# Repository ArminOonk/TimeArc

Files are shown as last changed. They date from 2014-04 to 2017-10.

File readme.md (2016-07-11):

# Preparing the raspberry pi

## Update and install packages
Use the following commands to get the RPi ready

	sudo apt-get remove --purge desktop-base lightdm lxappearance lxde-common lxde-icon-theme lxinput lxpanel lxpolkit lxrandr lxsession-edit lxshortcut lxtask lxterminal
	sudo apt-get remove --purge obconf openbox raspberrypi-artwork 
	sudo apt-get remove --purge xarchiver xinit xserver-xorg 
	sudo apt-get remove --purge xserver-xorg-video-fbdev x11-utils x11-common x11-session utils
	sudo apt-get remove wolfram-*
	sudo apt-get update
	sudo apt-get upgrade
	sudo apt-get autoremove
	sudo rpi-update

# ESP Wifi
To get the esp wifi working first check the hardware. The APR2016 version has an error in the schematic. CH_PD is not connected to the correct pin.

In stall the driver using the instruction on the following website: http://oshlab.com/esp8266-raspberry-pi-gpio-wifi/

	cd ~
	git clone https://github.com/oshlab/esp8089.git
	cd esp8089
	sudo sh install
	sudo reboot
	sudo iwlist scan
	ifconfig

Check if wlan0 is visible. Now connect it to the wifi
	
	sudo nano /etc/wpa_supplicant/wpa_supplicant.conf

	network={
	ssid="testing"
	psk="testingPassword"
	}
	
Run the following commands if there is no internet connection (Test by using `ping 8.8.8.8`)

	sudo ifdown wlan0
	sudo ifup wlan0

# Install instructions

## Python packages
install pyfeed-0.7.4 and xe-0.7.4 from the Software directory

## Settings
Create a timearcPrivate.py file using the example

Add the following lines to /etc/rc.local

	sleep 30
	/home/pi/timearc/Software/startup

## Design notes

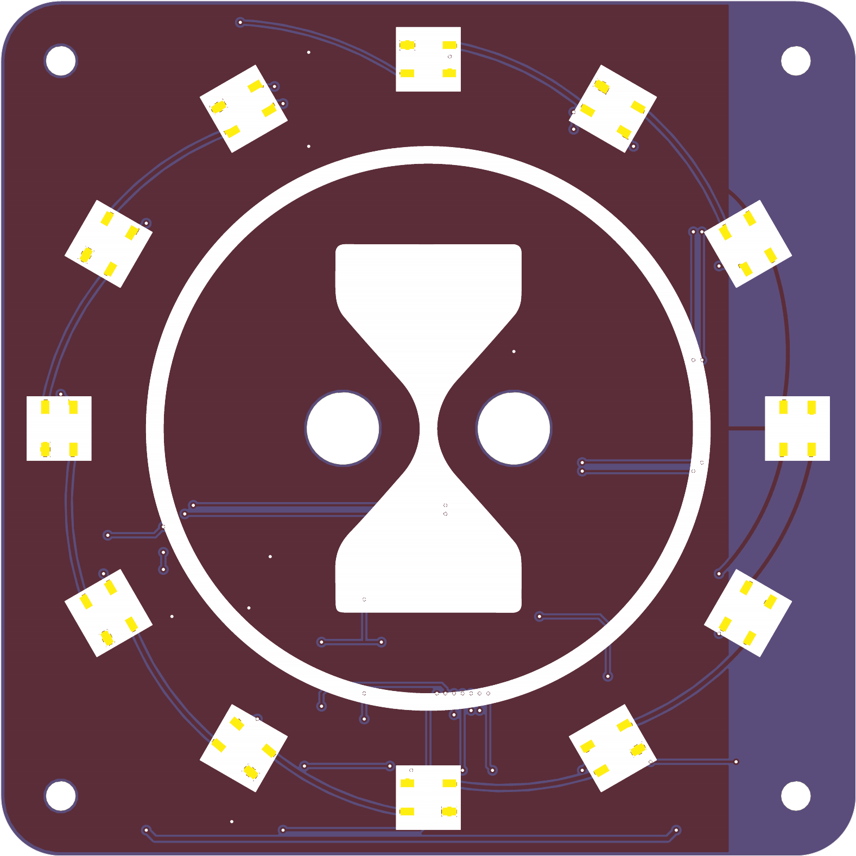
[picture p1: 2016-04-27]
Hardware/Back2016/Back2016_Bottom.png

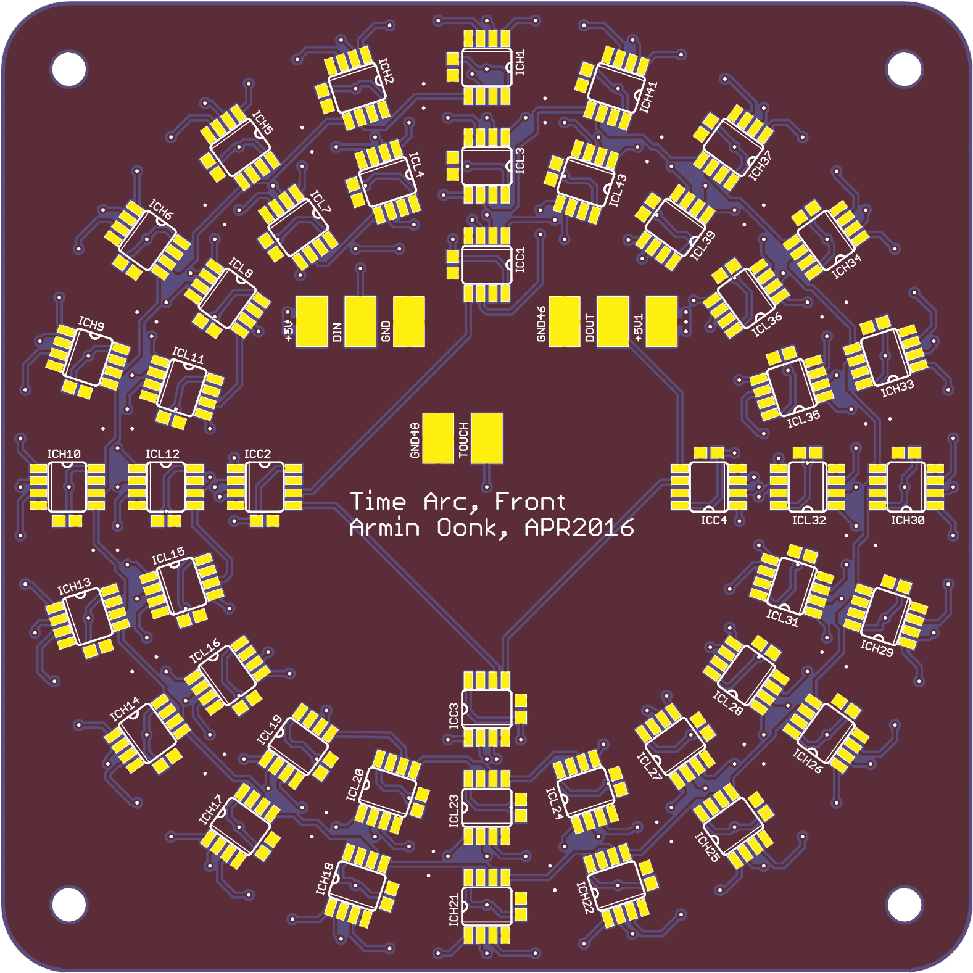
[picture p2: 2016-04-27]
Hardware/Front2016/Front2016_Top.png

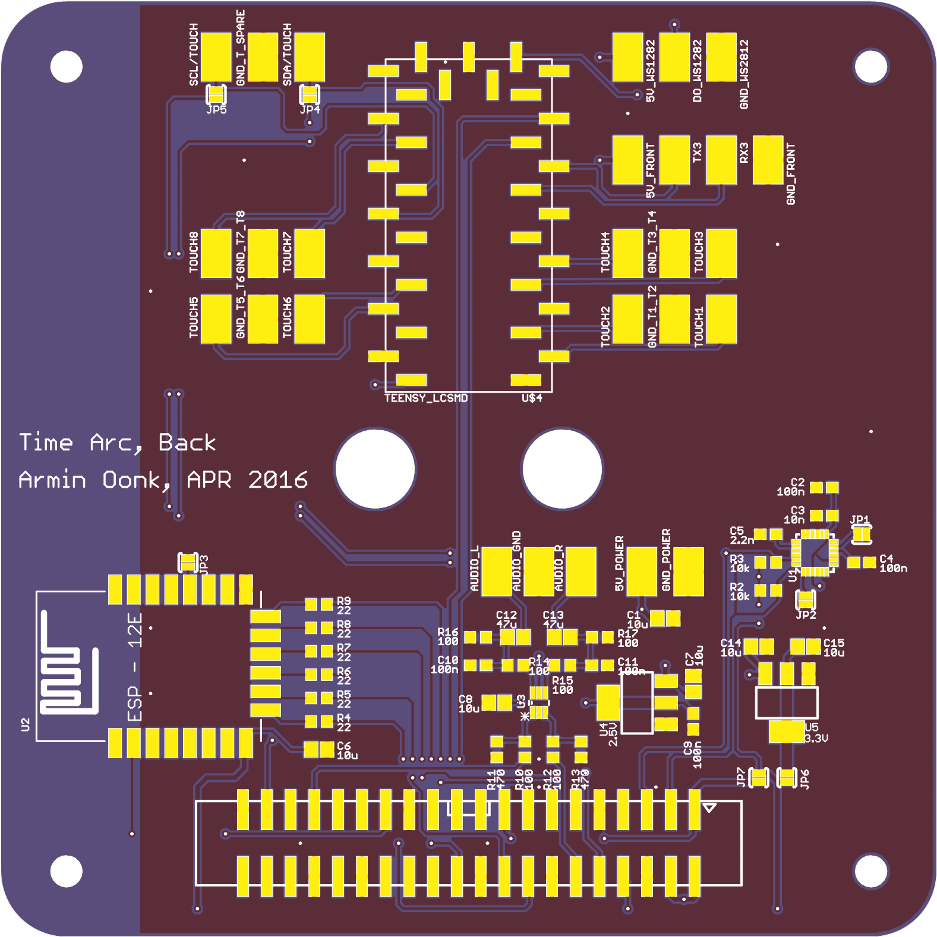
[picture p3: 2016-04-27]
Hardware/Back2016/Back2016_Top.png

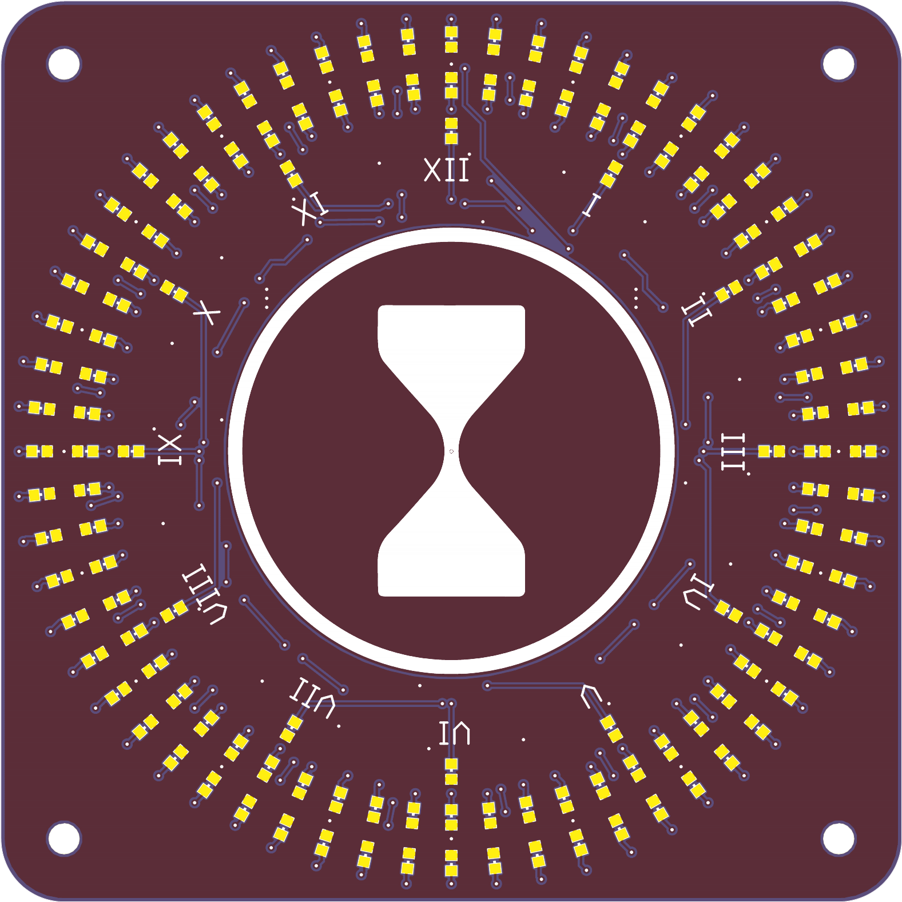
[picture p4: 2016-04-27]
Hardware/Front2016/Front2016_Bottom.png

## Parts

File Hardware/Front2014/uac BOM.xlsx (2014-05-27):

Qty | Part | Value | Description | MPN | OC_DIGIKEY_1 | OC_FARNELL | U_PRICE_1 | Price total
1 | C1 | 100n | CAPACITOR, European symbol |  |  | 1759016 | €0.01 | €0.01
1 | C2 | 100n | CAPACITOR, European symbol |  |  | 1759016 | €0.01 | €0.01
1 | C3 | 100n | CAPACITOR, European symbol |  |  | 1759016 | €0.01 | €0.01
1 | C4 | 100n | CAPACITOR, European symbol |  |  | 1759016 | €0.01 | €0.01
1 | C5 | 100n | CAPACITOR, European symbol |  |  | 1759016 | €0.01 | €0.01
1 | C6 | 6.8p | CAPACITOR, European symbol |  |  | 1856099 | €0.03 | €0.03
1 | C7 | 6.8p | CAPACITOR, European symbol |  |  | 1856099 | €0.03 | €0.03
1 | C8 | 10u | CAPACITOR, European symbol |  |  | 1759393 | €0.12 | €0.12
1 | C11 | 100n | CAPACITOR, European symbol |  |  | 1759016 | €0.01 | €0.01
1 | C17 | 10u | CAPACITOR, European symbol |  |  | 1759393 | €0.12 | €0.12
1 | C18 | 100n | CAPACITOR, European symbol |  |  | 1759016 | €0.01 | €0.01
1 | C20 | 10n | CAPACITOR, European symbol |  |  | 1759102 | €0.01 | €0.01
1 | C23 | 10u | CAPACITOR, European symbol |  |  | 1759393 | €0.12 | €0.12
1 | C24 | 100u | POLARIZED CAPACITOR, European symbol |  |  | 1907361 | €1.84 | €1.84
1 | C25 | 100u | POLARIZED CAPACITOR, European symbol |  |  | 1907361 | €1.84 | €1.84
1 | C27 | 10u | CAPACITOR, European symbol |  |  | 1759393 | €0.12 | €0.12
1 | FTDI |  | Header 6 |  |  | 2084270 | €1.22 | €1.22
12 | HOUR0 |  | LED |  |  | 8529841 | €0.28 | €3.36
1 | IC1 |  | Voltage Regulator LM1117 |  |  | 1469051 | €1.23 | €1.23
60 | MIN0 |  | LED |  |  | 8529868 | €0.20 | €12.00
1 | PROG |  | PIN HEADER |  |  | 2056005 | €0.45 | €0.45
1 | Q1 | 2N7002CK4SST | N-Channel JFETs |  |  | 1829183 | €0.37 | €0.37
1 | Q6 | 2N7002CK4SST | N-Channel JFETs |  |  | 1798076 | €0.02 | €0.02
1 | Q7 | 2N7002CK4SST | N-Channel JFETs |  |  | 1798076 | €0.02 | €0.02
1 | R1 |  | RESISTOR, European symbol |  |  | 2073347 | €0.01 | €0.01
1 | R2 |  | RESISTOR, European symbol |  |  | 2073347 | €0.01 | €0.01
1 | R3 |  | RESISTOR, European symbol |  |  | 2073347 | €0.01 | €0.01
1 | R4 |  | RESISTOR, European symbol |  |  | 2073347 | €0.01 | €0.01
1 | R5 |  | RESISTOR, European symbol |  |  | 2073347 | €0.01 | €0.01
1 | R6 |  | RESISTOR, European symbol |  |  | 2073347 | €0.01 | €0.01
1 | R7 |  | RESISTOR, European symbol |  |  | 2073347 | €0.01 | €0.01
1 | R8 |  | RESISTOR, European symbol |  |  | 2073347 | €0.01 | €0.01
1 | R9 |  | RESISTOR, European symbol |  |  | 2073347 | €0.01 | €0.01
1 | R10 |  | RESISTOR, European symbol |  |  | 2073347 | €0.01 | €0.01
1 | R11 |  | RESISTOR, European symbol |  |  | 2073347 | €0.01 | €0.01
1 | R12 |  | RESISTOR, European symbol |  |  | 2073347 | €0.01 | €0.01
1 | R13 | 0 | RESISTOR, European symbol |  |  | 2309106 | €0.0047 | €0.0047
1 | R16 | 10k | RESISTOR, European symbol |  |  | 1469748 | €0.02 | €0.02
1 | R23 | 10k | RESISTOR, European symbol |  |  | 1469748 | €0.02 | €0.02
1 | R27 | 10k | RESISTOR, European symbol |  |  | 1469748 | €0.02 | €0.02
1 | R28 | 0 | RESISTOR, European symbol |  |  | 2309106 | €0.0047 | €0.0047
1 | R29 | 0 | RESISTOR, European symbol |  |  | 2309106 | €0.0047 | €0.0047
1 | R30 | 1k5 | RESISTOR, European symbol |  |  | 2073391 | €0.01 | €0.01
1 | R31 | 10k | RESISTOR, European symbol |  |  | 1469748 | €0.02 | €0.02
1 | R32 | 10k | RESISTOR, European symbol |  |  | 1469748 | €0.02 | €0.02
1 | R33 | 36k | RESISTOR, European symbol |  |  | 2138459 | €0.01 | €0.01
1 | R34 | 47k | RESISTOR, European symbol |  |  | 2073515 | €0.01 | €0.01
1 | R36 | 10k | RESISTOR, European symbol |  |  | 1469748 | €0.02 | €0.02
1 | R43 | 10k | RESISTOR, European symbol |  |  | 1469748 | €0.02 | €0.02
60 | SEC0 |  | LED |  |  | 2213649 | €0.20 | €11.94
60 |  |  |  |  |  | 2251459 | €0.09 | €5.52
60 |  |  |  |  |  | 2217978 | €0.13 | €8.04
1 | SPECIAL0 |  | LED |  |  |  |  | €0.00
1 | SPECIAL3 |  | LED |  |  |  |  | €0.00
1 | SPECIAL5 |  | LED |  |  |  |  | €0.00
1 | SPECIAL6 |  | LED |  |  |  |  | €0.00
1 | SPECIAL9 |  | LED |  |  |  |  | €0.00
1 | SPECIAL11 |  | LED |  |  |  |  | €0.00
1 | U$1 | STM32F103CBT6 |  |  |  | 1447640 | €5.71 | €5.71
1 | U$2 | CRYSTAL_32KHZ |  | MC-306 32.768K-E3:ROHS | SER2417TR-ND |  |  | €0.00
1 | U$11 | KDT0030 | Updated Light Sensor | KDT00030TR | KDT00030FSCT-ND |  | €0.60 | €0.60
1 | U$12 | USB-MINIB-5PIN | Mini-USB B" connector with 5th pin broken out." |  |  | 1125348 | €0.56 | €0.56
1 | U$13 | USBLC6-2SC6 |  | USBLC6-2SC6 |  | 1269406 | €0.76 | €0.76
1 | U2 | ADXL345 |  |  |  | 1853935 | €5.38 | €5.38
1 | Y1 | RESONATORSMD | Resonator |  | 490-1198-1-ND | 1615352 | €0.80 | €0.80
4 |  | spacers m3x40 |  |  |  | 1466833 | €0.48 | €1.92
 |  |  |  |  |  |  | Total | €64.46

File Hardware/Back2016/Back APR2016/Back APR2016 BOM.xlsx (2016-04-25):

Part | Value | Device | Description | Manufacturer | MPN | OC_FARNELL | Link
C1 | 10u | C-EUC0805 | CAPACITOR, European symbol |  |  | 2320856
C2 | 100n | C-EUC0603 | CAPACITOR, European symbol |  |  | 2496832
C3 | 10n | C-EUC0603 | CAPACITOR, European symbol |  |  | 2496826
C4 | 100n | C-EUC0603 | CAPACITOR, European symbol |  |  | 2496832
C5 | 2.2n | C-EUC0603 | CAPACITOR, European symbol |  |  | 2496845
C6 | 10u | C-EUC0805 | CAPACITOR, European symbol |  |  | 2320856
C7 | 10u | C-EUC0805 | CAPACITOR, European symbol |  |  | 2320856
C8 | 10u | C-EUC0805 | CAPACITOR, European symbol |  |  | 2320856
C9 | 100n | C-EUC0603 | CAPACITOR, European symbol |  |  | 2496832
C10 | 100n | C-EUC0603 | CAPACITOR, European symbol |  |  | 2496832
C11 | 100n | C-EUC0603 | CAPACITOR, European symbol |  |  | 2496832
C12 | 47u | C-EUC0805 | CAPACITOR, European symbol |  |  | 2362109
C13 | 47u | C-EUC0805 | CAPACITOR, European symbol |  |  | 2362109
C14 | 10u | C-EUC0805 | CAPACITOR, European symbol |  |  | 2320856
C15 | 10u | C-EUC0805 | CAPACITOR, European symbol |  |  | 2320856
J1 | RASPBERRYPI-40-PIN-GPIO-SMT | RASPBERRYPI-40-PIN-GPIO-SMT | Second Generation Raspberry Pi GPIO Header |  |  | 1256663
LED1 | WS2812B5050 | WS2812B5050 |  |  |  |  | http://www.aliexpress.com/item/10-1000pcs-WS2812B-4pins-5050-SMD-Black-White-version-WS2812-Individually-Addressable-Digital-RGB-LED-Chip/32453497583.html
LED2 | WS2812B5050 | WS2812B5050 |  |  |  |  | http://www.aliexpress.com/item/10-1000pcs-WS2812B-4pins-5050-SMD-Black-White-version-WS2812-Individually-Addressable-Digital-RGB-LED-Chip/32453497583.html
LED3 | WS2812B5050 | WS2812B5050 |  |  |  |  | http://www.aliexpress.com/item/10-1000pcs-WS2812B-4pins-5050-SMD-Black-White-version-WS2812-Individually-Addressable-Digital-RGB-LED-Chip/32453497583.html
LED4 | WS2812B5050 | WS2812B5050 |  |  |  |  | http://www.aliexpress.com/item/10-1000pcs-WS2812B-4pins-5050-SMD-Black-White-version-WS2812-Individually-Addressable-Digital-RGB-LED-Chip/32453497583.html
LED5 | WS2812B5050 | WS2812B5050 |  |  |  |  | http://www.aliexpress.com/item/10-1000pcs-WS2812B-4pins-5050-SMD-Black-White-version-WS2812-Individually-Addressable-Digital-RGB-LED-Chip/32453497583.html
LED6 | WS2812B5050 | WS2812B5050 |  |  |  |  | http://www.aliexpress.com/item/10-1000pcs-WS2812B-4pins-5050-SMD-Black-White-version-WS2812-Individually-Addressable-Digital-RGB-LED-Chip/32453497583.html
LED7 | WS2812B5050 | WS2812B5050 |  |  |  |  | http://www.aliexpress.com/item/10-1000pcs-WS2812B-4pins-5050-SMD-Black-White-version-WS2812-Individually-Addressable-Digital-RGB-LED-Chip/32453497583.html
LED8 | WS2812B5050 | WS2812B5050 |  |  |  |  | http://www.aliexpress.com/item/10-1000pcs-WS2812B-4pins-5050-SMD-Black-White-version-WS2812-Individually-Addressable-Digital-RGB-LED-Chip/32453497583.html
LED9 | WS2812B5050 | WS2812B5050 |  |  |  |  | http://www.aliexpress.com/item/10-1000pcs-WS2812B-4pins-5050-SMD-Black-White-version-WS2812-Individually-Addressable-Digital-RGB-LED-Chip/32453497583.html
LED10 | WS2812B5050 | WS2812B5050 |  |  |  |  | http://www.aliexpress.com/item/10-1000pcs-WS2812B-4pins-5050-SMD-Black-White-version-WS2812-Individually-Addressable-Digital-RGB-LED-Chip/32453497583.html
LED11 | WS2812B5050 | WS2812B5050 |  |  |  |  | http://www.aliexpress.com/item/10-1000pcs-WS2812B-4pins-5050-SMD-Black-White-version-WS2812-Individually-Addressable-Digital-RGB-LED-Chip/32453497583.html
LED12 | WS2812B5050 | WS2812B5050 |  |  |  |  | http://www.aliexpress.com/item/10-1000pcs-WS2812B-4pins-5050-SMD-Black-White-version-WS2812-Individually-Addressable-Digital-RGB-LED-Chip/32453497583.html
R2 | 10k | R-EU_R0603 | RESISTOR, European symbol |  |  | 1469748
R3 | 10k | R-EU_R0603 | RESISTOR, European symbol |  |  | 1469748
R4 | 22 | R-EU_R0603 | RESISTOR, European symbol |  |  | 9330844
R5 | 22 | R-EU_R0603 | RESISTOR, European symbol |  |  | 9330844
R6 | 22 | R-EU_R0603 | RESISTOR, European symbol |  |  | 9330844
R7 | 22 | R-EU_R0603 | RESISTOR, European symbol |  |  | 9330844
R8 | 22 | R-EU_R0603 | RESISTOR, European symbol |  |  | 9330844
R9 | 22 | R-EU_R0603 | RESISTOR, European symbol |  |  | 9330844
R10 | 100 | R-EU_R0603 | RESISTOR, European symbol |  |  | 2130776
R11 | 470 | R-EU_R0603 | RESISTOR, European symbol |  |  | 2447374
R12 | 100 | R-EU_R0603 | RESISTOR, European symbol |  |  | 2130776
R13 | 470 | R-EU_R0603 | RESISTOR, European symbol |  |  | 2447374
R14 | 100 | R-EU_R0603 | RESISTOR, European symbol |  |  | 2130776
R15 | 100 | R-EU_R0603 | RESISTOR, European symbol |  |  | 2130776
R16 | 100 | R-EU_R0603 | RESISTOR, European symbol |  |  | 2130776
R17 | 100 | R-EU_R0603 | RESISTOR, European symbol |  |  | 2130776
U$4 | TEENSY_LCSMD | TEENSY_LCSMD | Teensy LC |  |  | 2356213
U1 |  | MPU-9150QFN-24-NP | 9DOF (3mag, 3accel, 3rotat). I2C interface. |  |  |  | http://www.aliexpress.com/item/Free-shipping-1pcs-lot-MPU-9150-MPU9150/32565889824.html
U2 |  | ESP12ESMD | ESP12E Module |  |  |  | http://www.aliexpress.com/item/2015-New-version-1PCS-ESP-12F-ESP-12E-upgrade-ESP8266-remote-serial-Port-WIFI-wireless-module/32590584160.html
U3 | SN74LVC2G34DCKR | SN74LVC2G34DCKR | DUAL BUFFER GATE |  | SN74LVC2G34DCKR | 1595409
U4 | 2.5V | V_REG_LM1117SOT223 | Voltage Regulator LM1117 |  |  | 1564629
U5 | 3.3V | V_REG_LM1117SOT223 | Voltage Regulator LM1117 |  |  | 1469051
 |  |  | Power jack panel mount |  |  | 1216726
 |  |  | Jack 3.5 mm panel mount |  |  | 1267396
Solder PADS
5V_FRONT | SOLDER_PAD | SOLDER_PAD
5V_POWER | SOLDER_PAD | SOLDER_PAD
5V_WS1282 | SOLDER_PAD | SOLDER_PAD
AUDIO_GND | SOLDER_PAD | SOLDER_PAD
AUDIO_L | SOLDER_PAD | SOLDER_PAD
AUDIO_R | SOLDER_PAD | SOLDER_PAD
DO_WS1282 | SOLDER_PAD | SOLDER_PAD
GND_FRONT | SOLDER_PAD | SOLDER_PAD
GND_POWER | SOLDER_PAD | SOLDER_PAD
GND_T1_T2 | SOLDER_PAD | SOLDER_PAD
GND_T3_T4 | SOLDER_PAD | SOLDER_PAD
GND_T5_T6 | SOLDER_PAD | SOLDER_PAD
GND_T7_T8 | SOLDER_PAD | SOLDER_PAD
GND_T_SPARE | SOLDER_PAD | SOLDER_PAD
GND_WS2812 | SOLDER_PAD | SOLDER_PAD
RX3 | SOLDER_PAD | SOLDER_PAD
SCL/TOUCH | SOLDER_PAD | SOLDER_PAD
SDA/TOUCH | SOLDER_PAD | SOLDER_PAD
TOUCH1 | SOLDER_PAD | SOLDER_PAD
TOUCH2 | SOLDER_PAD | SOLDER_PAD
TOUCH3 | SOLDER_PAD | SOLDER_PAD
TOUCH4 | SOLDER_PAD | SOLDER_PAD
TOUCH5 | SOLDER_PAD | SOLDER_PAD
TOUCH6 | SOLDER_PAD | SOLDER_PAD
TOUCH7 | SOLDER_PAD | SOLDER_PAD
TOUCH8 | SOLDER_PAD | SOLDER_PAD
TX3 | SOLDER_PAD | SOLDER_PAD
Jumpers
JP1 | JUMPER-PAD-2-NOYES_SILK | JUMPER-PAD-2-NOYES_SILK
JP2 | JUMPER-PAD-2-NOYES_SILK | JUMPER-PAD-2-NOYES_SILK
JP3 | JUMPER-PAD-2-NOYES_SILK | JUMPER-PAD-2-NOYES_SILK
JP4 | JUMPER-PAD-2-NOYES_SILK | JUMPER-PAD-2-NOYES_SILK
JP5 | JUMPER-PAD-2-NOYES_SILK | JUMPER-PAD-2-NOYES_SILK
JP6 | JUMPER-PAD-2-NOYES_SILK | JUMPER-PAD-2-NOYES_SILK
JP7 | JUMPER-PAD-2-NOYES_SILK | JUMPER-PAD-2-NOYES_SILK

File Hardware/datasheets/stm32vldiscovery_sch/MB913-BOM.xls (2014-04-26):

MB913 BOM
NO | Code | Part Number | Manufacturer | Description | Designator | Quantity | Process | Note
1 | 3ST0003 |  | FASTPRINT | PCB,MB913C |  | 1 | SMT
2 | ADL0002 | 316102S111A | LWCONN | Short ,open 2.54MM,1UGold,LWCONN；Harwin,M7566-05/M7571-05 |  | 3 | ASS
3 | AKG0002 | SH-517 Blue | szalong | key Cap,Blue,MB672 | B1-1 | 1 | ASS
4 | AKG0003 | SH-517Black | szalong | key Cap,Black,MB672 | B2-1 | 1 | ASS
5 | CCC0009 | CC0603KRX5R7BB105 | YAGEO | Capacitance,1uF,10%,16V,X5R,0603 | C16 | 1 | SMT
6 | CCC0049 | CC0603JRNPO9BN200 | YAGEO | Capacitance,20pF,5%,50V,NPO,0603 | C13,C12,C8,C9 | 4 | SMT
7 | CCC0071 | CC0402KRX7R7BB104 | YAGEO | Capacitance,0.1uF,10%,16V,X7R,0402 | C18,C19 | 2 | SMT
8 | CCC0188 | CC0603CRNPO9BN6R8 | YAGEO | Capacitance，0603，NPO,50V ±0.25PF 6P8F | C17,C11 | 2 | SMT
9 | CCC0194 | CC0603KRX7R7BB104 | YAGEO | Capacitance,0.1uF,10%,16V,X7R,0603 | C23,C3,C21,C20, C15,C7,C4,C10,C6,C5 | 10 | SMT
10 | CTD0045 | TAJA105K016R | AVX | Tantalum capacitor,1uF,10%,16V,AType,AVX | C14 | 1 | SMT
11 | CTD0099 | TAJA106K016RNJ | AVX | Tantalum capacitor,10uF,10%,16V,AType,AVX | C1,C2 | 2 | SMT
12 | DEJ0018 | BZX84-C5V6 | NXP | Diode，BZX84-C5V6，5.6V,SOT23,NXP | D3,D4 | 2 | SMT
13 | DLD0027 | 19-213-RC-AP1Q2B-3T | EVERLIGHT | LED,red,0603,19-213-RC-AP1Q2B-3T,LED | LD2,LD1 | 2 | SMT
14 | DLD0028 | 19-213SY6C/5530-E2/TR8 | EVERLIGHT | LED,Green,0603,19-213SY6C/5530-E2/TR8,LED | LD3 | 1 | SMT
15 | DLD0029 | 19-217/BHC-ZL1M2RY/3T | EVERLIGHT | LED,blue,0603,19-217/BHC-ZL1M2RY/3T,LED | LD4 | 1 | SMT
16 | JJZ0001 | PIN-E740 | LWCONN | Stilt,7.4Circular apertureCrystal oscillatorFoot,1PIN,Golden,DIP,PIN-E740，LWCONN | X2-1，X2-2 | 2 | DIP
17 | JPZ0015 | 313140S212116 | LWCONN | Row,2.54mm,1*4,L=11.6,180Degree,3UGold,DIP,LWCONN | CN2,CN3 | 8/40 | DIP
18 | JPZ0015 | 313140S212116 | LWCONN | Row,2.54mm,1*2,L=11.6,180Degree,3UGold,DIP,LWCONN | JP1 | 2/40 | DIP
19 | JPZ0032 | 313128S212145 | LWCONN | Row,2.54mm,1*28P,180Degree,L=14.5,Plating3UGold,SMT,LWCONN | P1,P2 | 2 | SMT
20 | JPZ0033 | 313140S212145 | LWCONN | Row,2.54mm,1*6P,180Degree,L=14.5,Plating3UGold,SMT,LWCONN | P3 | 6/40 | SMT
21 | JUS0021 | MUSB5QS-BM1H6-NLB-E | townes | USB,MUSB5QS-BM1H6-NLB-E,townes | CN1 | 1 | SMT
22 | LCZ0006 | FCM1608KF-601T03 | Tai-tech | 600R,350mA,0603,FCM1608KF-601T03,Tai-tech | L1 | 1 | SMT
23 | PBQ0004 |  |  | label,18*6mm,MB913C | label | 1 | ASS
24 | PBQ0016 |  |  | Test label，CharacterT1,T2,T3,T4,QA,see Sample |  | 1 | ASS
25 | PKZ0003 |  |  | The ST standard cardboardMB913,93*135mm,STStandard Edition | packing | 1 | ASS
26 | PKZ0008 |  |  | The ST standard cardboardMB913,93*135mm,EBVEdition | packing | 1 | ASS
27 | PKZ0009 |  |  | The ST standard cardboardMB913,93*135mm,XL Edition | packing | 1 | ASS
28 | PKZ0010 |  |  | The ST standard cardboardMB913,93*135mm,ARROW Edition | packing | 1 | ASS
29 | PKZ0011 |  |  | The ST standard cardboardMB913,93*135mm,Silica Edition | packing | 1 | ASS
30 | PKZ0012 |  |  | The ST standard cardboardMB913,93*135mm,Farnell Edition | packing | 1 | ASS
31 | PSD0001 | TZ-211 |  | Label，Black text on a white background，6mm,8m | Label | 1/450 | ASS
32 | PXS0001 |  |  | MB913 blister,PET0.5mm, | packing | 1 | ASS
33 | PZB0001 |  |  | Cardboard，605*415mm | box | 1/50 | ASS
34 | PZX0006 |  |  | box，L620*425*310mm | box | 150/1 | ASS
35 | RRC0023 | RC0805JR-070RL | YAGEO | Resistance,0R,5%,0805 | R22 | 1 | SMT
36 | RRC0029 | RC0603JR-07100RL | YAGEO | Resistance,100R,1%,0603 | R20 | 1 | SMT
37 | RRC0030 | RC0603JR-070RL | YAGEO | Resistance,0R,5%,0603 | R15 | 1 | SMT
38 | RRC0220 | RC0402JR-070RL | YAGEO | Resistance,0R,5%,0402 | SB1,SB2,SB3,SB5,SB7,SB9,SB11,SB16,SB17,SB18 | 10 | SMT
39 | RRC0224 | RC0402JR-071K5L | YAGEO | Resistance,1.5K,1%,0402 | R2 | 1 | SMT
40 | RRC0301 | RC0402JR-0722RL | YAGEO | Resistance,22R,1%,0402 | R4,R3,R11,R12 | 4 | SMT
41 | RRC0328 | RC0603FR-07665RL | YAGEO | Resistance，665R,1%,0603 | R26 | 1 | SMT
42 | RRC0374 | RC0603JR-07820RL | YAGEO | Resistance,820R,1%,0603 | R23 | 1 | SMT
43 | RRC0379 | RC0603JR-07100KL | YAGEO | Resistance,100K,1%,0603 | R1 | 1 | SMT
44 | RRC0387 | RC0603JR-07330RL | YAGEO | Resistance,330R,1%,0603 | R25 | 1 | SMT
45 | RRC0388 | RC0603JR-07220KL | YAGEO | Resistance,220K,1%,0603 | R21 | 1 | SMT
46 | RRC0402 | RC0402JR-074K7L | YAGEO | Resistance,4.7K,1%,0402 | R9,R10 | 2 | SMT
47 | RRC0403 | RC0603JR-07510RL | YAGEO | Resistance,510R,1%,0603 | R18,R16,R6 | 3 | SMT
48 | RRC0404 | RC0603JR-07220RL | YAGEO | Resistance,220R,1%,0603 | R14 | 1 | SMT
49 | RRC0411 | RC0402JR-071KL | YAGEO | Resistance,1K,1%,0402 | R5 | 1 | SMT
50 | RRC0412 | RC0402JR-07100KL | YAGEO | Resistance,100K,1%,0402 | R7,R13 | 2 | SMT
51 | RRC0413 | RC0402JR-0710KL | YAGEO | Resistance,10K,1%,0402 | R19,R17,R8 | 3 | SMT
52 | SQC0001 | TD0341X-G01-BLU | wealthmetal | Switch,Touch switch,blue,Square head,6*6,SMT,180Degree，TD-0341X-GO1,wealthmetal | B1 | 1 | SMT
53 | SQC0002 | TD0341X-G01-BLA | wealthmetal | Switch,Touch switch,Black,Square head,6*6,SMT,180Degree，TD-0341X-GO1,wealthmetal | B2 | 1 | SMT
54 | ST-DEJ0010 | BAT60JFILM | ST | Diode,BAT60JFILM,SOD323/A,ST | D1,D2 | 2 | SMT
55 | ST-UIC0013 | STM32F100RBT6B | ST | IC,MCU,STM32F100RBT6B，LQFP64,ST,MB913B | U3 | 1 | SMT
56 | ST-UIC0034 | LD1117DT33TR | ST | IC,Voltage regulatorIC,3.3V,DPAK,LD1117DT33TR,ST | U1 | 1 | SMT
57 | ST-UIC0107 | STM32F103C8T6 | ST | IC,CPU,STM32F103C8T6,LQFP48,ST | U2 | 1 | SMT
58 | XWY0010 | MC-306-G06Q-32.768 | jfvny | Crystal oscillator,32.768K,6PF,20PPM,-10~60Degree,SMT,MC306-B06Q-32.768,jfvny | X3 | 1 | SMT
59 | XWY0022 | HC-49S-B20QTA-8.0000 | jfvny | Crystal oscillator,8M,20PF,20PPM,-10~60Degree,DIP,HC-49S-B20QTA-8.0000,jfvny | X2 | 1 | DIP
60 | XWY0022 | HC-49S-B20QTA-8.0000 | jfvny | Crystal oscillator,8M,20PF,20PPM,-10~60Degree,DIP,HC-49S-B20QTA-8.0000,jfvny | X1 | 1 | DIP

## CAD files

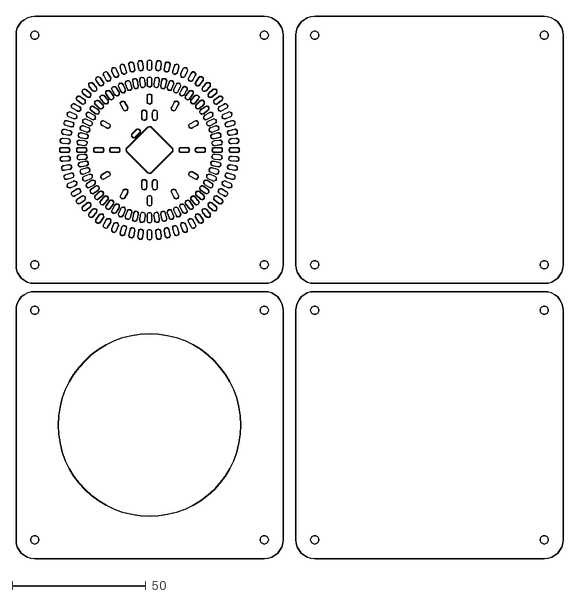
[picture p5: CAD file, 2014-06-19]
Hardware/LaserCutFront2014/lasercutAssembly.dxf
204.8 x 203.0

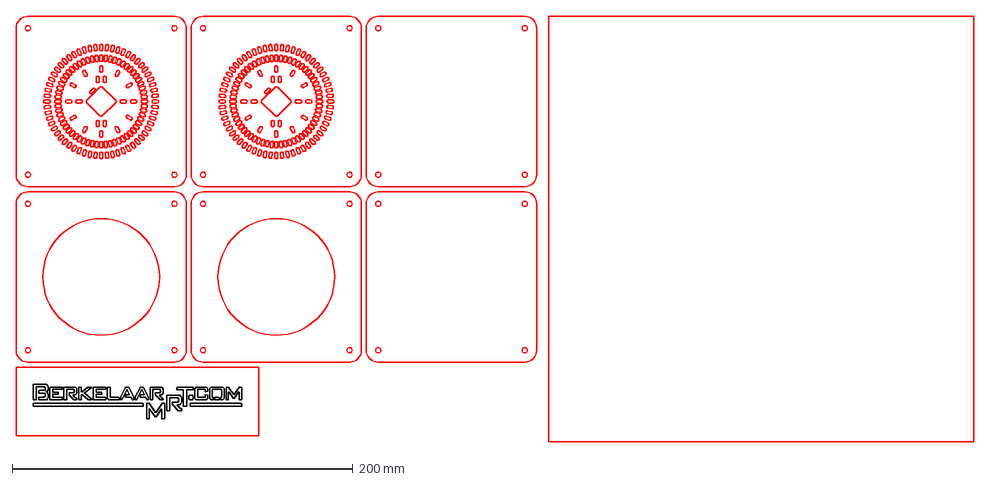
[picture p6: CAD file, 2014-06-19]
Hardware/LaserCutFront2014/lasercut_dxf_2004.dxf
562.4 x 249.8 mm

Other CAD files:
Enclosure/Enclosure.skp
Enclosure/OrderDangerousPrototypes.skp

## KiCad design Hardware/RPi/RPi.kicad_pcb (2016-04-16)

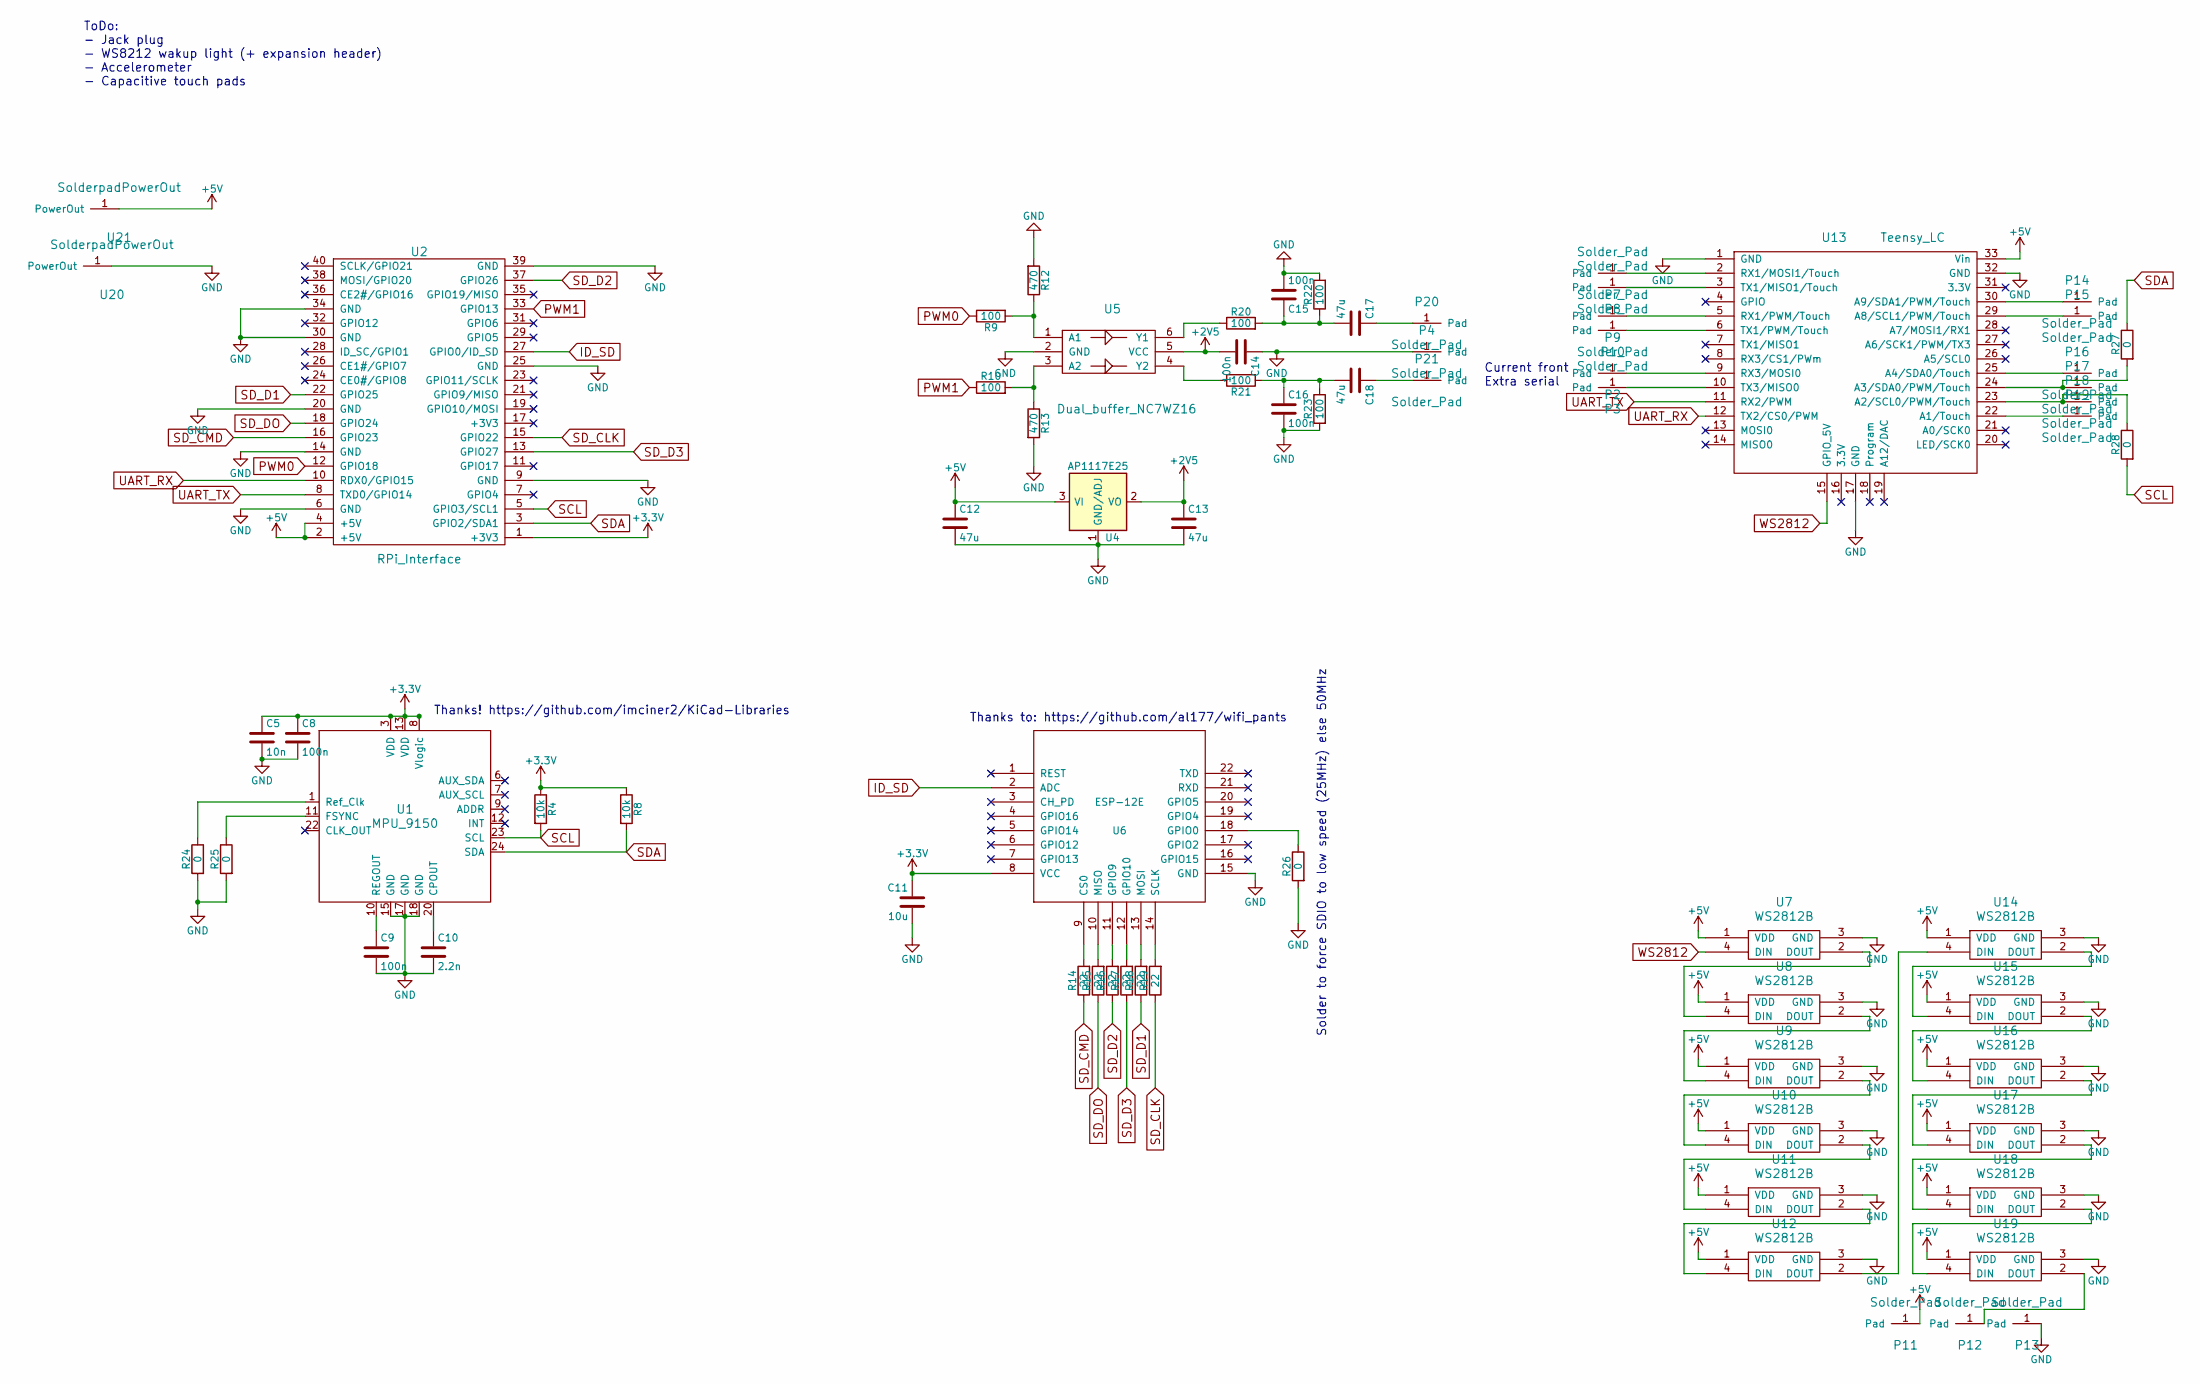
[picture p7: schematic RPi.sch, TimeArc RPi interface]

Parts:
C5: 10n; C_0603
C8, C9, C14, C15, C16: 100n; C_0603
C10: 2.2n; C_0603
C11: 10u; C_0603
C12, C13, C17, C18: 47u; C_0805
P2, P3, P4, P7, P8, P9, P10, P11, P12, P13, P14, P15, P16, P17, P18, P19, P20, P21: Solder_Pad; Measurement_Point_Square-SMD-Pad_Big
R4, R8: 10k; R_0603
R9, R10, R20, R21, R22, R23: 100; R_0603
R12, R13: 470; R_0603
R14, R15, R16, R17, R18, R19: 22; R_0603
R24, R25, R26, R27, R28: 0; R_0603
U1: MPU_9150; IMU9150
U2: RPi_Interface; RPi_Zero_farnell_1256663
U4: AP1117E25; SOT-223
U5: Dual_buffer_NC7WZ16; SC-70-6_Handsoldering
U6: ESP-12E
U7, U8, U9, U10, U11, U12, U14, U15, U16, U17, U18, U19: WS2812B; PLCC4-5050
U13: Teensy_LC; TeensyLC
U20, U21: SolderpadPowerOut; Measurement_Point_Square-SMD-Pad_Big

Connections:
+2V5: C13.1, C14.2, U4.2 (VO), U5.5 (VCC)
+3V3: C5.1, C8.1, C11.1, R4.1, R8.1, U1.3 (VDD), U1.8 (Vlogic), U1.13 (VDD), U2.1 (+3V3), U6.8 (VCC)
+5V: C12.1, P11.1, U2.2 (+5V), U2.4 (+5V), U4.3 (VI), U7.1 (VDD), U8.1 (VDD), U9.1 (VDD), U10.1 (VDD), U11.1 (VDD), U12.1 (VDD), U13.33 (Vin), U14.1 (VDD), U15.1 (VDD), U16.1 (VDD), U17.1 (VDD), U18.1 (VDD), U19.1 (VDD), U21.1
GND: C5.2, C8.2, C9.2, C10.2, C11.2, C12.2, C13.2, C14.1, C15.2, C16.2, P4.1, P13.1, R12.2, R13.2, R22.2, R23.2, R24.2, R25.2, R26.2, U1.15 (GND), U1.17 (GND), U1.18 (GND), U2.6 (GND), U2.9 (GND), U2.14 (GND), U2.20 (GND), U2.25 (GND), U2.30 (GND), U2.34 (GND), U2.39 (GND), U4.1 (GND/ADJ), U5.2 (GND), U6.15 (GND), U7.3 (GND), U8.3 (GND), U9.3 (GND), U10.3 (GND), U11.3 (GND), U12.3 (GND), U13.1 (GND), U13.17 (GND), U13.32 (GND), U14.3 (GND), U15.3 (GND), U16.3 (GND), U17.3 (GND), U18.3 (GND), U19.3 (GND), U20.1
ID_SD: U2.27 (GPIO0/ID_SD), U6.2 (ADC)
unnamed: C9.1, U1.10 (REGOUT)
unnamed: C10.1, U1.20 (CPOUT)
unnamed: C15.1, C17.2, R20.2, R22.1
unnamed: C16.1, C18.2, R21.2, R23.1
unnamed: C17.1, P20.1
unnamed: C18.1, P21.1
unnamed: P2.1, U13.9 (RX3/MOSI0)
unnamed: P3.1, U13.10 (TX3/MISO0)
unnamed: P7.1, U13.2 (RX1/MOSI1/Touch)
unnamed: P8.1, U13.3 (TX1/MISO1/Touch)
unnamed: P9.1, U13.5 (RX1/PWM/Touch)
unnamed: P10.1, U13.6 (TX1/PWM/Touch)
unnamed: P12.1, U19.2 (DOUT)
unnamed: P14.1, U13.30 (A9/SDA1/PWM/Touch)
unnamed: P15.1, U13.29 (A8/SCL1/PWM/Touch)
unnamed: P16.1, U13.25 (A4/SDA0/Touch)
unnamed: P17.1, R27.2, U13.24 (A3/SDA0/PWM/Touch)
unnamed: P18.1, R28.1, U13.23 (A2/SCL0/PWM/Touch)
unnamed: P19.1, U13.22 (A1/Touch)
unnamed: R10.2, R13.1, U5.3 (A2)
unnamed: R9.2, R12.1, U5.1 (A1)
unnamed: R14.2, U6.9 (CS0)
unnamed: R15.2, U6.10 (MISO)
unnamed: R16.2, U6.11 (GPIO9)
unnamed: R17.2, U6.12 (GPIO10)
unnamed: R18.2, U6.13 (MOSI)
unnamed: R19.2, U6.14 (SCLK)
unnamed: R20.1, U5.6 (Y1)
unnamed: R21.1, U5.4 (Y2)
unnamed: R24.1, U1.1 (Ref_Clk)
unnamed: R25.1, U1.11 (FSYNC)
unnamed: R26.1, U6.18 (GPIO0)
unnamed: U7.2 (DOUT), U8.4 (DIN)
unnamed: U8.2 (DOUT), U9.4 (DIN)
unnamed: U10.2 (DOUT), U11.4 (DIN)
unnamed: U9.2 (DOUT), U10.4 (DIN)
unnamed: U11.2 (DOUT), U12.4 (DIN)
unnamed: U12.2 (DOUT), U14.4 (DIN)
unnamed: U14.2 (DOUT), U15.4 (DIN)
unnamed: U15.2 (DOUT), U16.4 (DIN)
unnamed: U16.2 (DOUT), U17.4 (DIN)
unnamed: U17.2 (DOUT), U18.4 (DIN)
unnamed: U18.2 (DOUT), U19.4 (DIN)
PWM0: R9.1, U2.12 (GPIO18)
PWM1: R10.1, U2.33 (GPIO13)
SCL: R4.2, R28.2, U1.23 (SCL), U2.5 (GPIO3/SCL1)
SDA: R8.2, R27.1, U1.24 (SDA), U2.3 (GPIO2/SDA1)
SD_CLK: R19.1, U2.15 (GPIO22)
SD_CMD: R14.1, U2.16 (GPIO23)
SD_D1: R18.1, U2.22 (GPIO25)
SD_D2: R16.1, U2.37 (GPIO26)
SD_D3: R17.1, U2.13 (GPIO27)
SD_DO: R15.1, U2.18 (GPIO24)
UART_RX: U2.10 (RDX0/GPIO15), U13.12 (TX2/CS0/PWM)
UART_TX: U2.8 (TXD0/GPIO14), U13.11 (RX2/PWM)
WS2812: U7.4 (DIN), U13.15 (GPIO_5V)

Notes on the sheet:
Solder to force SDIO to low speed (25MHz) else 50MHz
Thanks to: https://github.com/al177/wifi_pants
ToDo: - Jack plug - WS8212 wakup light (+ expansion header) - Accelerometer - Capacitive touch pads
Thanks! https://github.com/imciner2/KiCad-Libraries
Current front Extra serial

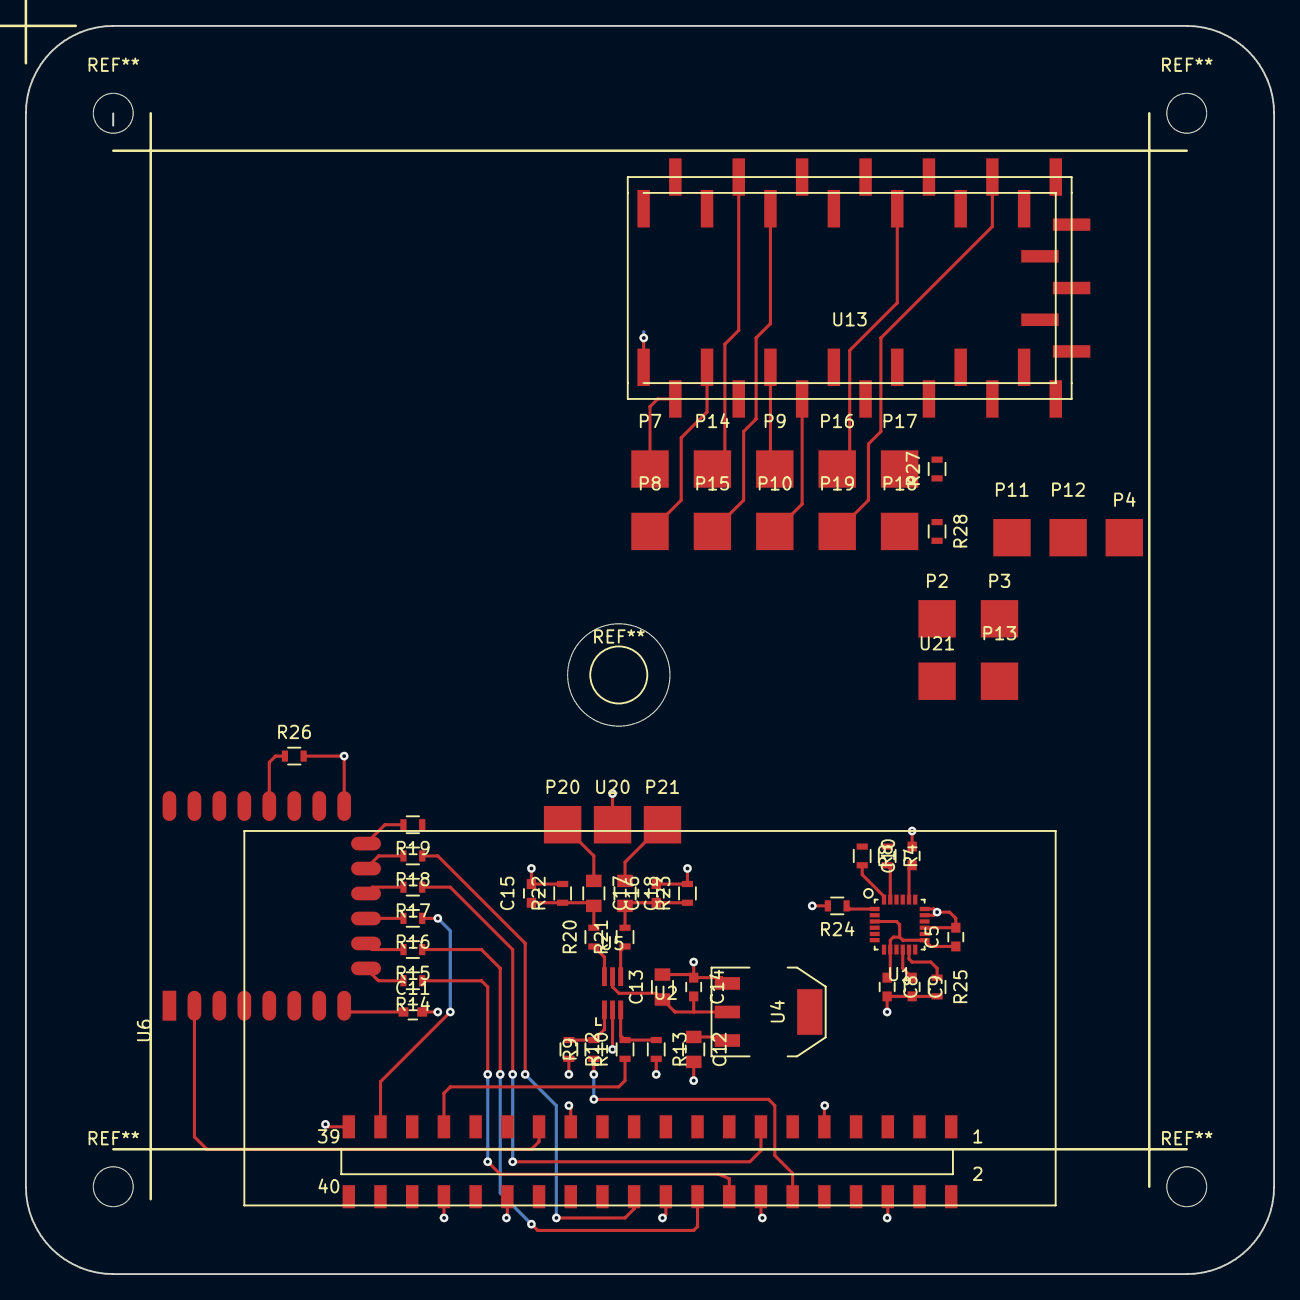
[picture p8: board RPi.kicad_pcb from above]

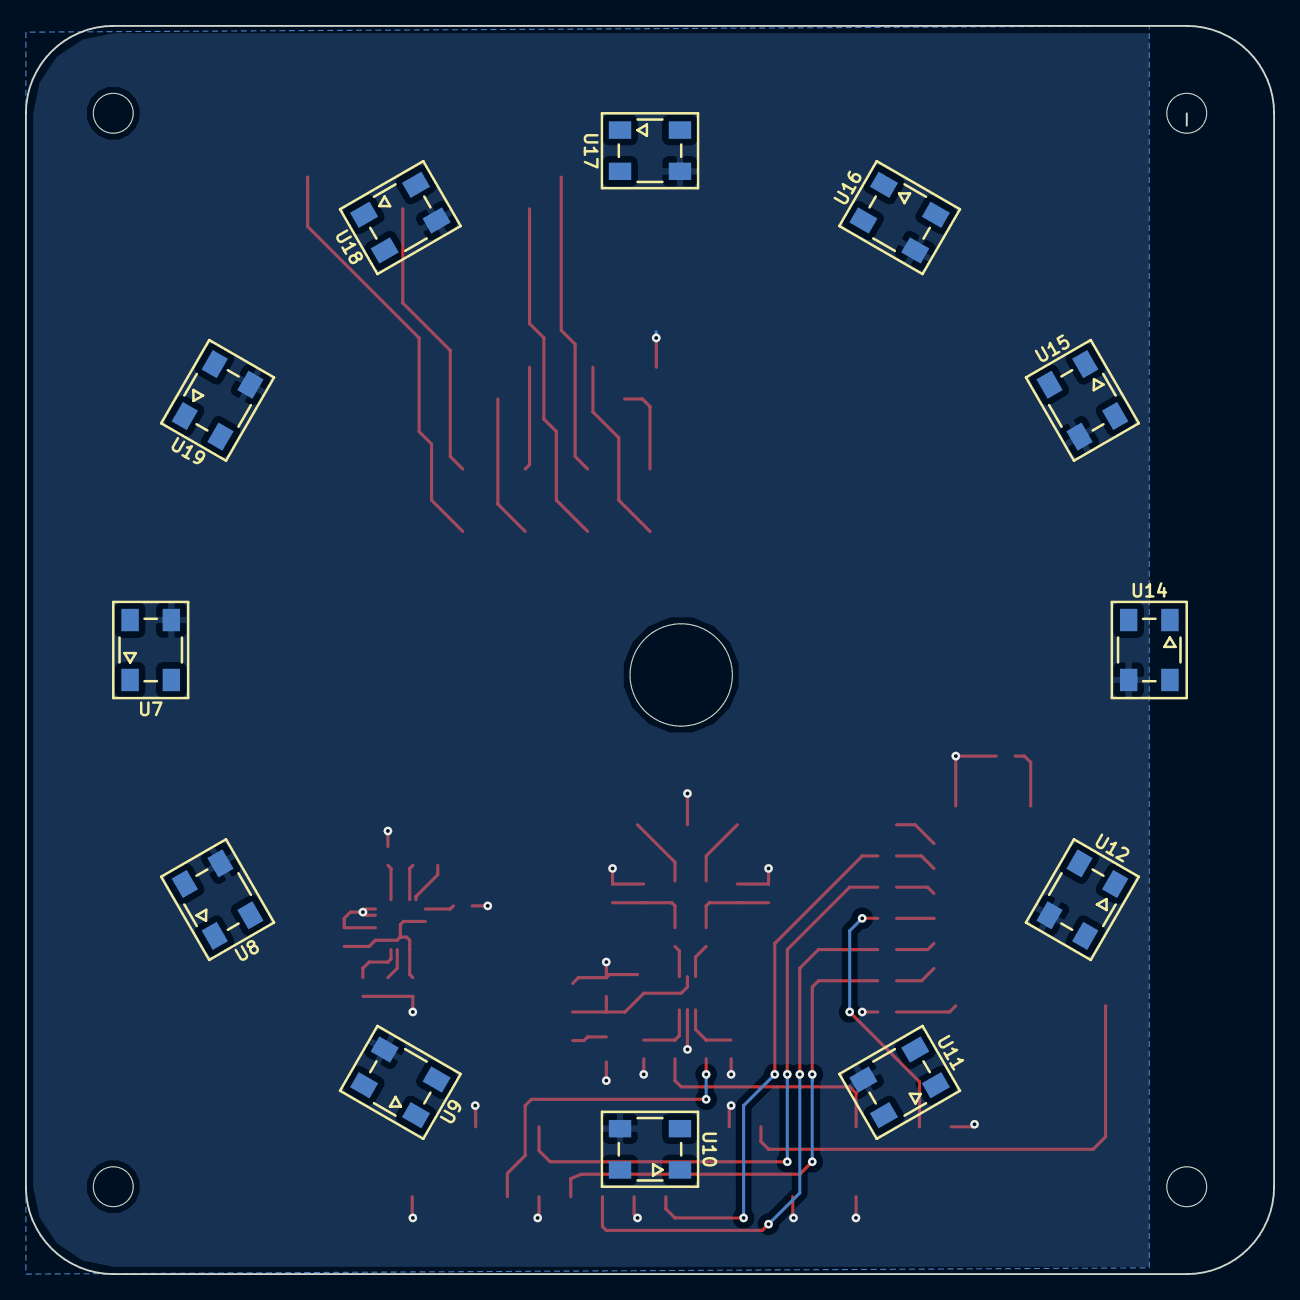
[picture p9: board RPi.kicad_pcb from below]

Board: 2 copper layers, 100.0 x 100.0 mm, 71 parts (12 on the bottom side), 61 nets.

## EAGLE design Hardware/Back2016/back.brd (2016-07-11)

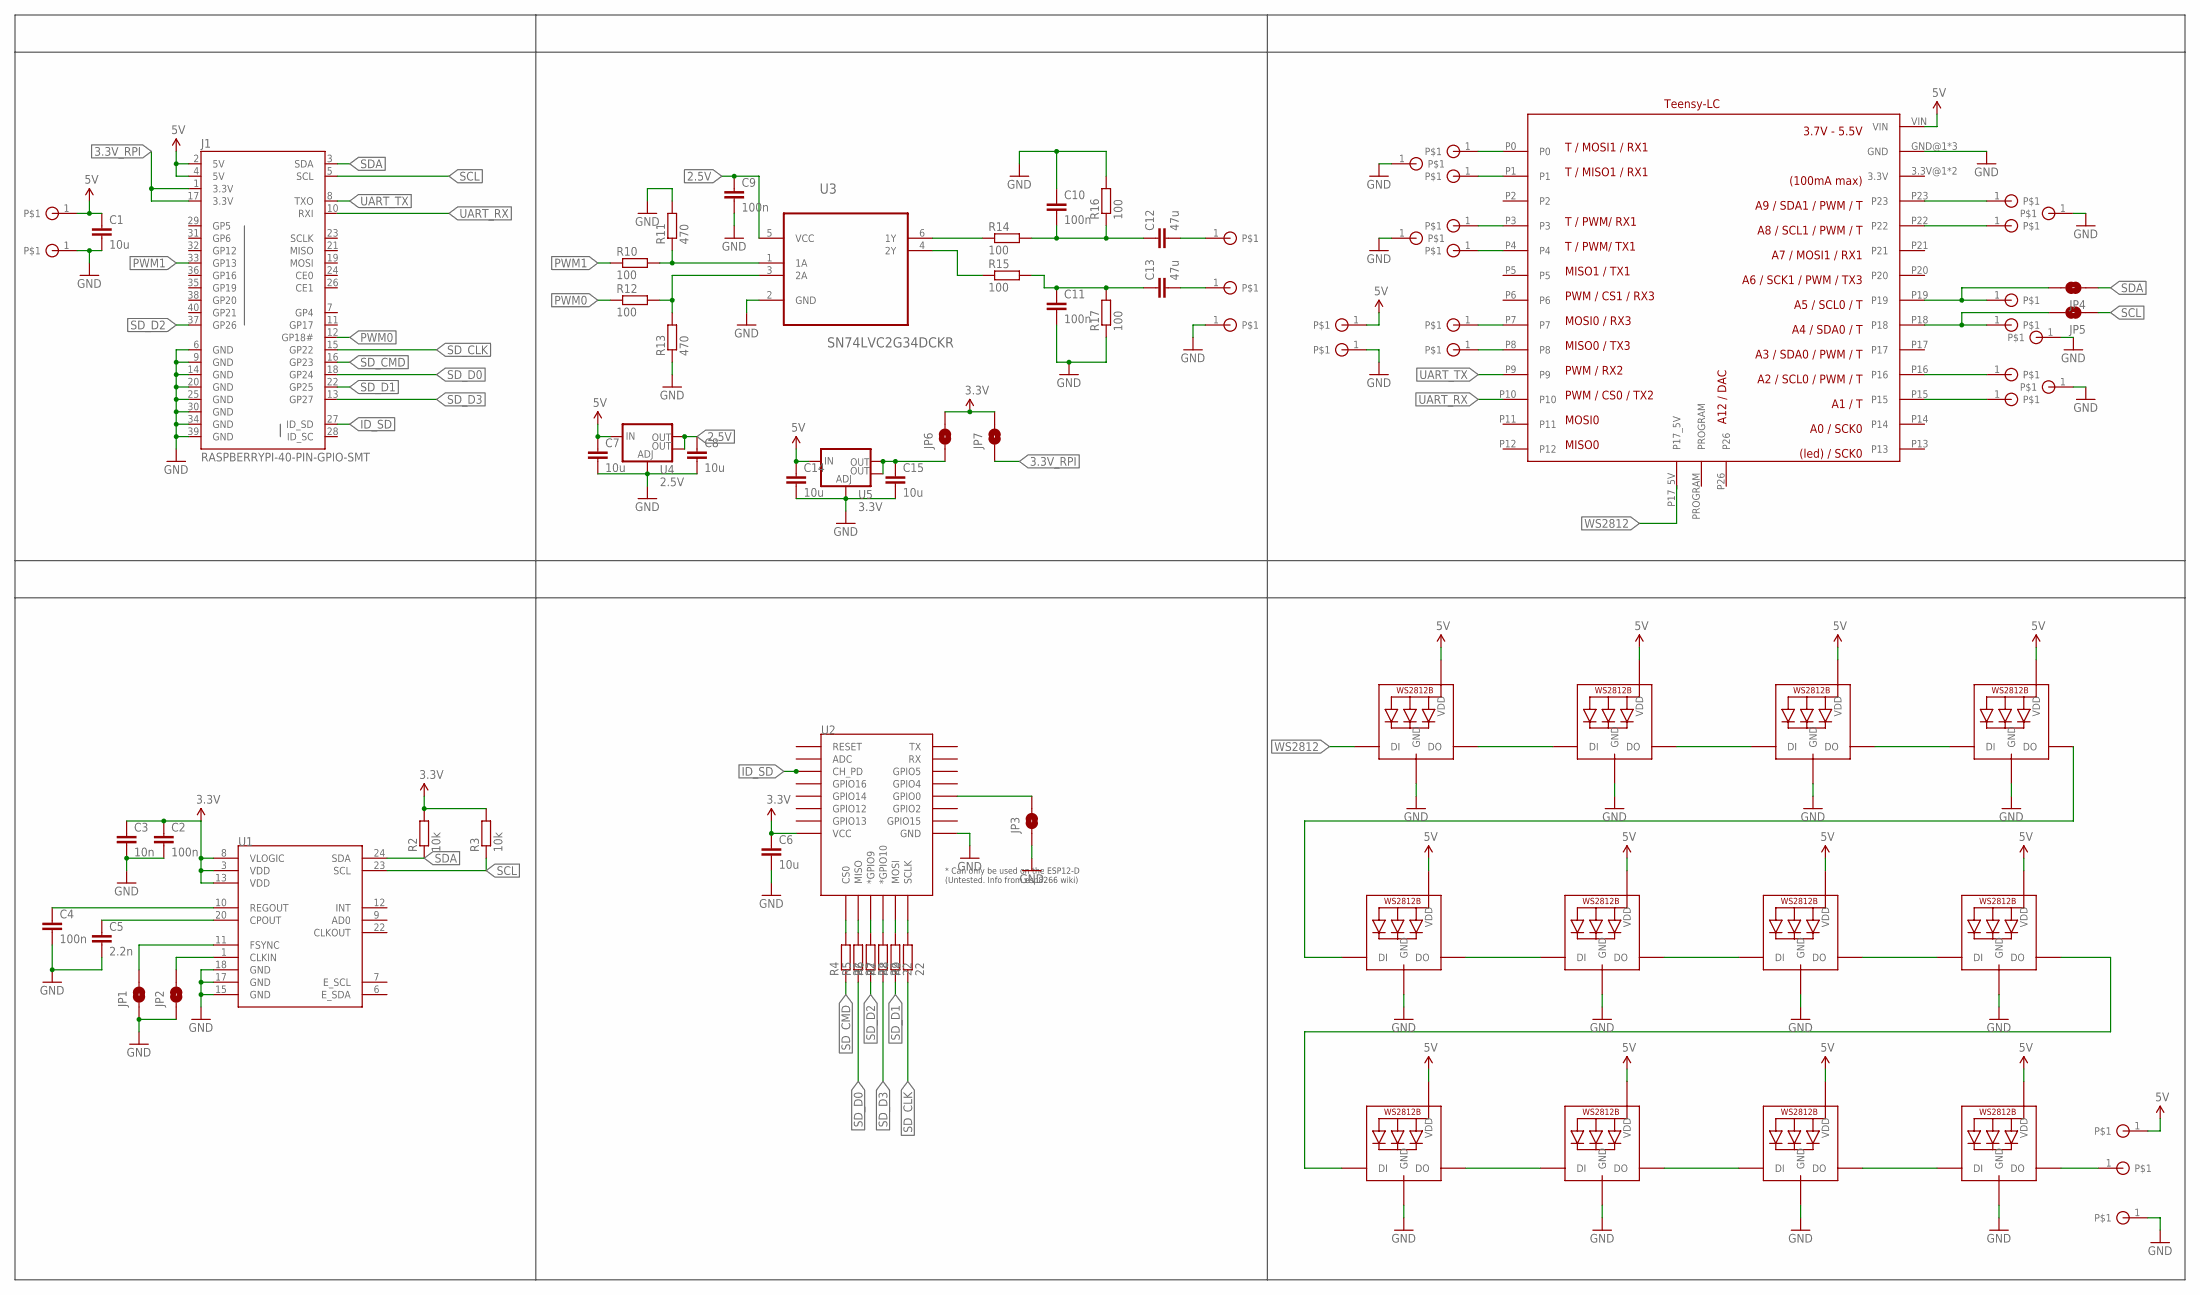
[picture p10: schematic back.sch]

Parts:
5V_FRONT, 5V_POWER, 5V_WS1282: SOLDER_PAD
AUDIO_GND: SOLDER_PAD
AUDIO_L: SOLDER_PAD
AUDIO_R: SOLDER_PAD
C1, C6, C7, C8, C14, C15: 10u; C0805
C2, C4, C9, C10, C11: 100n; C0603
C3: 10n; C0603
C5: 2.2n; C0603
C12, C13: 47u; C0805
DO_WS1282: SOLDER_PAD
GND_FRONT: SOLDER_PAD
GND_POWER: SOLDER_PAD
GND_T1_T2, GND_T3_T4, GND_T5_T6, GND_T7_T8: SOLDER_PAD
GND_T_SPARE: SOLDER_PAD
GND_WS2812: SOLDER_PAD
J1: RASPBERRYPI-40-PIN-GPIO-SMT; 2X20-SHROUDED-SMT
JP1, JP2, JP3, JP4, JP5, JP6, JP7: JUMPER-PAD-2-NOYES_SILK; PAD-JUMPER-2-NO_YES_SILK
LED1, LED2, LED3, LED4, LED5, LED6, LED7, LED8, LED9, LED10, LED11, LED12: WS2812B5050; WS2812B
R2, R3: 10k; R0603
R4, R5, R6, R7, R8, R9: 22; R0603
R10, R12, R14, R15, R16, R17: 100; R0603
R11, R13: 470; R0603
RX3: SOLDER_PAD
SCL/TOUCH: SOLDER_PAD
SDA/TOUCH: SOLDER_PAD
TOUCH1, TOUCH2, TOUCH3, TOUCH4, TOUCH5, TOUCH6, TOUCH7, TOUCH8: SOLDER_PAD
TX3: SOLDER_PAD
U1: MPU-9150QFN-24-NP; QFN-24-NP
U2: ESP12ESMD; ESP12E-SMD
U3: SN74LVC2G34DCKR; SOT65P210X110-6N
U4: 2.5V; SOT223
U5: 3.3V; SOT223
U$4: TEENSY_LCSMD; TEENSY_LC_SMD

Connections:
2.5V: C8.1, C9.1, U3.5 (VCC), U4.2 (OUT), U4.4 (OUT)
3.3V: C2.1, C3.1, C6.1, JP6.2, JP7.2, R2.2, R3.2, U1.3 (VDD), U1.8 (VLOGIC), U1.13 (VDD), U2.VCC
3.3V_RPI: J1.1 (3.3V), J1.17 (3.3V), JP7.1
5V: 5V_FRONT.1, 5V_POWER.1, 5V_WS1282.1, C1.1, C7.1, C14.1, J1.2 (5V), J1.4 (5V), LED1.1-VDD (VDD), LED2.1-VDD (VDD), LED3.1-VDD (VDD), LED4.1-VDD (VDD), LED5.1-VDD (VDD), LED6.1-VDD (VDD), LED7.1-VDD (VDD), LED8.1-VDD (VDD), LED9.1-VDD (VDD), LED10.1-VDD (VDD), LED11.1-VDD (VDD), LED12.1-VDD (VDD), U4.3 (IN), U5.3 (IN), U$4.VIN
GND: AUDIO_GND.1, C1.2, C2.2, C3.2, C4.2, C5.2, C6.2, C7.2, C8.2, C9.2, C10.1, C11.2, C14.2, C15.2, GND_FRONT.1, GND_POWER.1, GND_T1_T2.1, GND_T3_T4.1, GND_T5_T6.1, GND_T7_T8.1, GND_T_SPARE.1, GND_WS2812.1, J1.6 (GND), J1.9 (GND), J1.14 (GND), J1.20 (GND), J1.25 (GND), J1.30 (GND), J1.34 (GND), J1.39 (GND), JP1.1, JP2.1, JP3.1, LED1.3-GND (GND), LED2.3-GND (GND), LED3.3-GND (GND), LED4.3-GND (GND), LED5.3-GND (GND), LED6.3-GND (GND), LED7.3-GND (GND), LED8.3-GND (GND), LED9.3-GND (GND), LED10.3-GND (GND), LED11.3-GND (GND), LED12.3-GND (GND), R11.2, R13.1, R16.2, R17.1, U1.15 (GND), U1.17 (GND), U1.18 (GND), U2.GND, U3.2 (GND), U4.1 (ADJ), U5.1 (ADJ), U$4.GND@1 (GND), U$4.GND@2 (GND), U$4.GND@3 (GND)
ID_SD: J1.27 (ID_SD), U2.CH_PD
unnamed: JP2.2, U1.1 (CLKIN)
unnamed: JP1.2, U1.11 (FSYNC)
unnamed: C5.1, U1.20 (CPOUT)
unnamed: C4.1, U1.10 (REGOUT)
unnamed: R14.1, U3.6 (1Y)
unnamed: R4.2, U2.CS0
unnamed: R5.2, U2.MISO
unnamed: R6.2, U2.GPIO9 (*GPIO9)
unnamed: R7.2, U2.GPIO10 (*GPIO10)
unnamed: R8.2, U2.MOSI
unnamed: R9.2, U2.SCLK
unnamed: JP3.2, U2.GPIO0
unnamed: R10.2, R11.1, U3.1 (1A)
unnamed: R12.2, R13.2, U3.3 (2A)
unnamed: R15.1, U3.4 (2Y)
unnamed: C10.2, C12.1, R14.2, R16.1
unnamed: C11.1, C13.1, R15.2, R17.2
unnamed: LED1.2-DOUT (DO), LED2.4-DIN (DI)
unnamed: AUDIO_L.1, C12.2
unnamed: AUDIO_R.1, C13.2
unnamed: TOUCH1.1, U$4.P0
unnamed: TOUCH2.1, U$4.P1
unnamed: TOUCH3.1, U$4.P3
unnamed: TOUCH4.1, U$4.P4
unnamed: TOUCH5.1, U$4.P23
unnamed: TOUCH6.1, U$4.P22
unnamed: JP4.2, SDA/TOUCH.1, U$4.P19
unnamed: JP5.2, SCL/TOUCH.1, U$4.P18
unnamed: TOUCH7.1, U$4.P16
unnamed: TOUCH8.1, U$4.P15
unnamed: RX3.1, U$4.P7
unnamed: TX3.1, U$4.P8
unnamed: LED2.2-DOUT (DO), LED3.4-DIN (DI)
unnamed: LED3.2-DOUT (DO), LED4.4-DIN (DI)
unnamed: LED4.2-DOUT (DO), LED5.4-DIN (DI)
unnamed: LED5.2-DOUT (DO), LED6.4-DIN (DI)
unnamed: LED6.2-DOUT (DO), LED7.4-DIN (DI)
unnamed: LED7.2-DOUT (DO), LED8.4-DIN (DI)
unnamed: LED8.2-DOUT (DO), LED9.4-DIN (DI)
unnamed: LED9.2-DOUT (DO), LED10.4-DIN (DI)
unnamed: LED10.2-DOUT (DO), LED11.4-DIN (DI)
unnamed: LED11.2-DOUT (DO), LED12.4-DIN (DI)
unnamed: DO_WS1282.1, LED12.2-DOUT (DO)
unnamed: C15.1, JP6.1, U5.2 (OUT), U5.4 (OUT)
PWM0: J1.12 (GP18#), R12.1
PWM1: J1.33 (GP13), R10.1
SCL: J1.5 (SCL), JP5.1, R3.1, U1.23 (SCL)
SDA: J1.3 (SDA), JP4.1, R2.1, U1.24 (SDA)
SD_CLK: J1.15 (GP22), R9.1
SD_CMD: J1.16 (GP23), R4.1
SD_D0: J1.18 (GP24), R5.1
SD_D1: J1.22 (GP25), R8.1
SD_D2: J1.37 (GP26), R6.1
SD_D3: J1.13 (GP27), R7.1
UART_RX: J1.10 (RXI), U$4.P10
UART_TX: J1.8 (TXO), U$4.P9
WS2812: LED1.4-DIN (DI), U$4.P17_5V

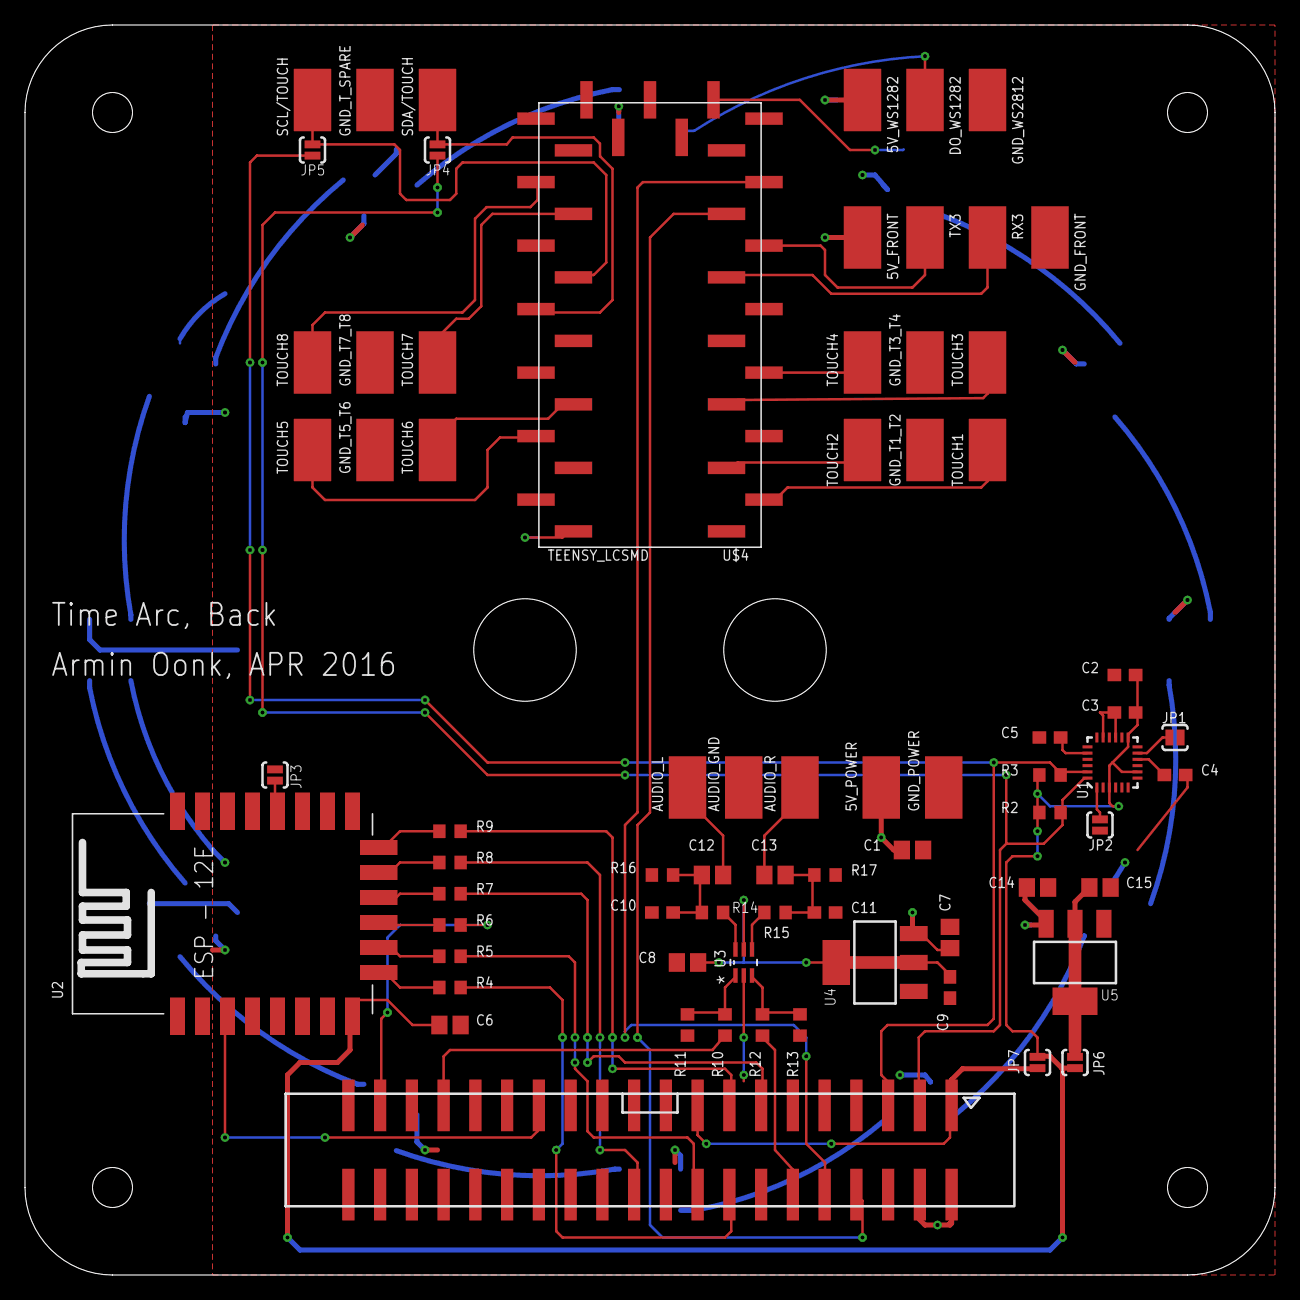
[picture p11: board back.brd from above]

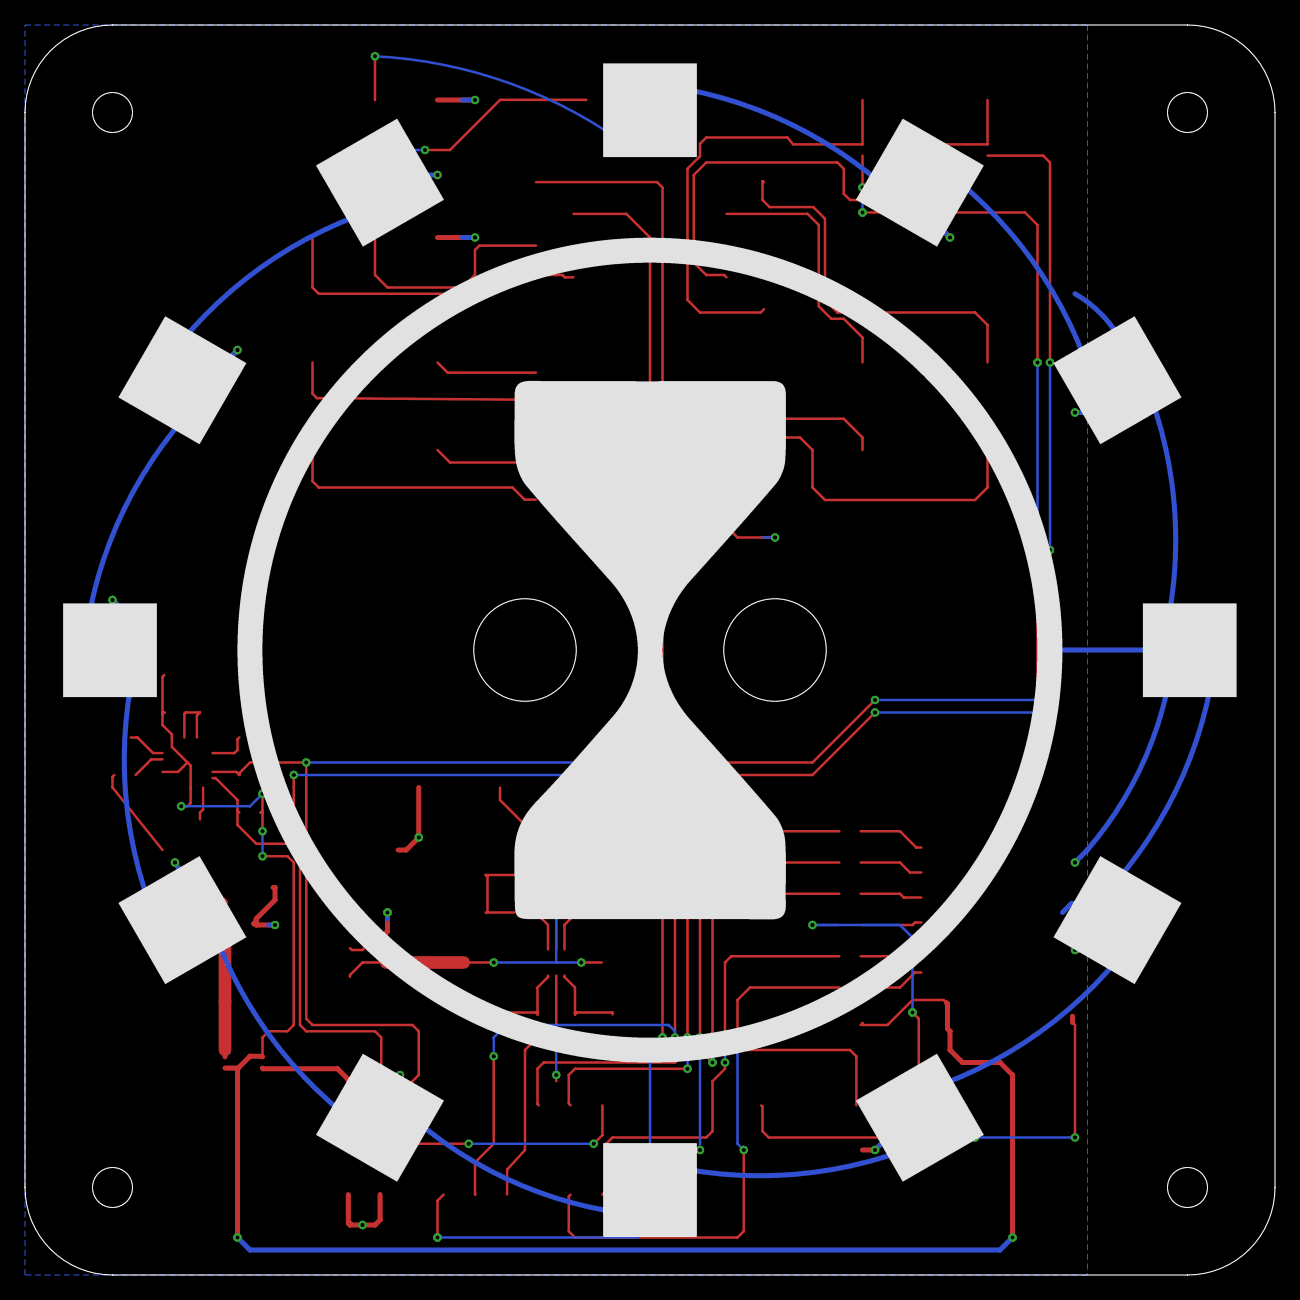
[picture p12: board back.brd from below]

Board: 2 copper layers, 100.0 x 100.0 mm, 86 parts (13 on the bottom side), 63 nets.

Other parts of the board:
U$1: TIMEARC_LOGO
U$15: TIMEARC_KEEPOUT

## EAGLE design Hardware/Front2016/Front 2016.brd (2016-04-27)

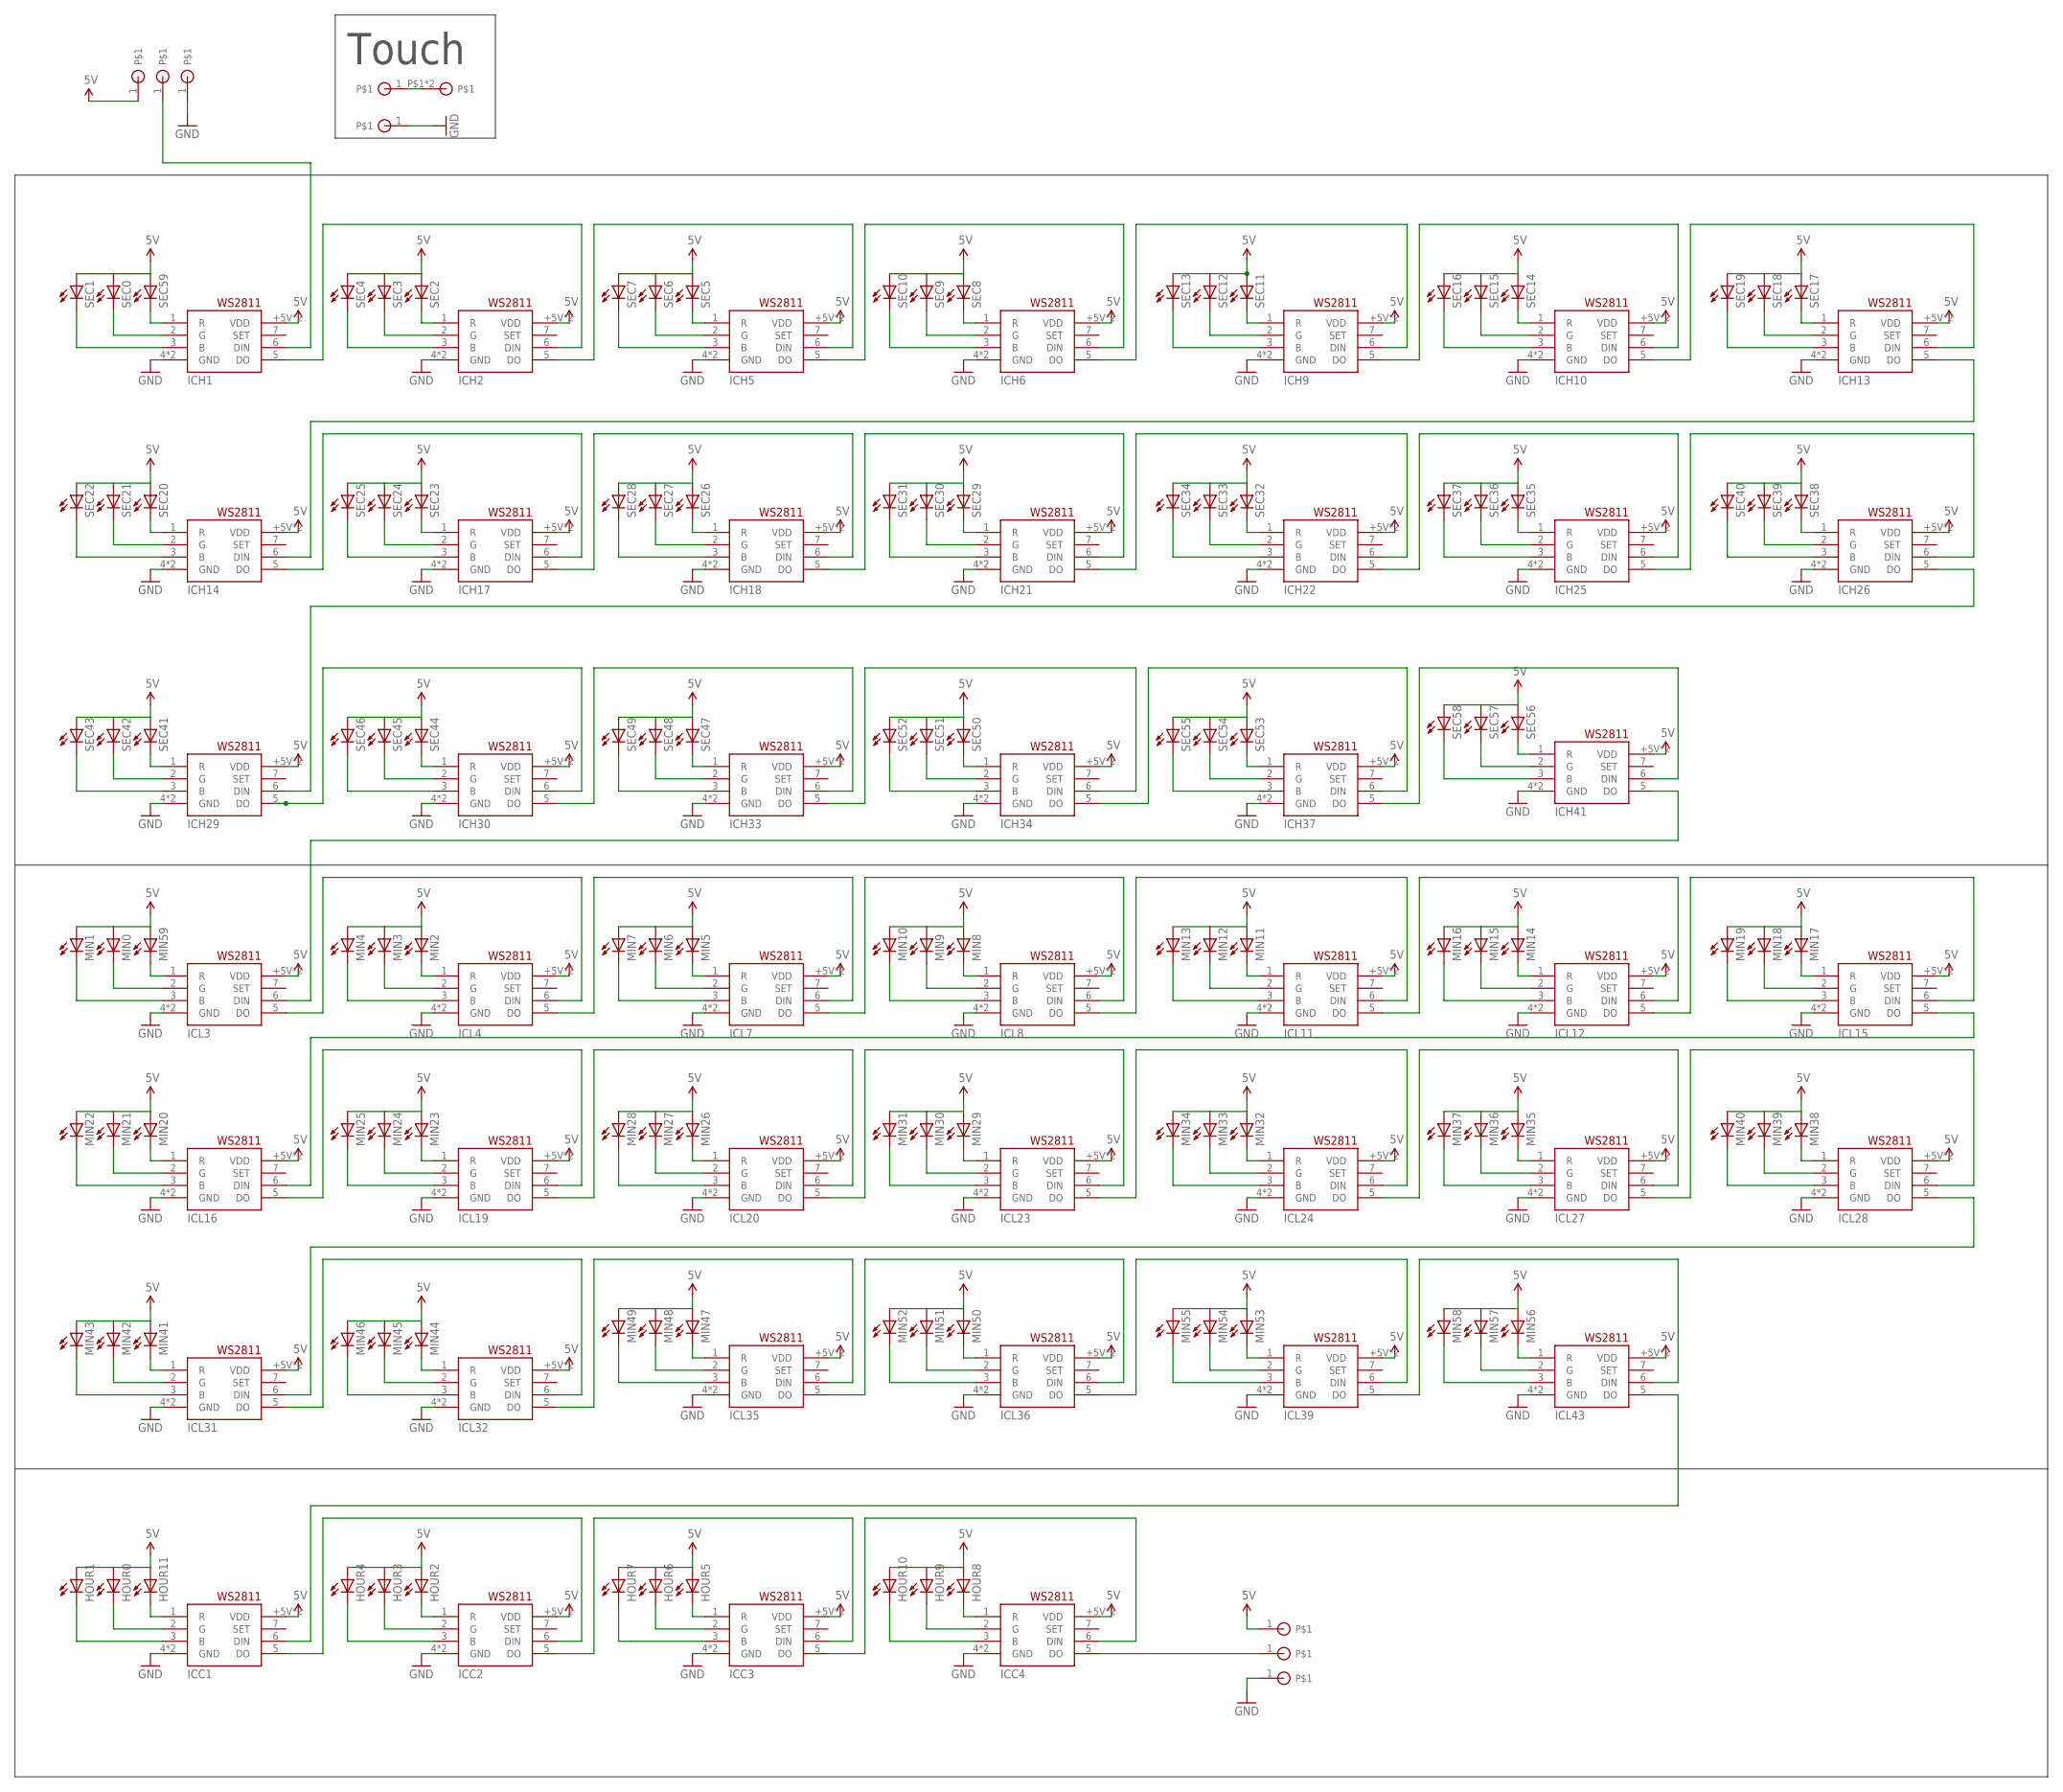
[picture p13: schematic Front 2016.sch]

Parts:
+5V, +5V1: SOLDER_PAD
DIN: SOLDER_PAD
DOUT: SOLDER_PAD
GND, GND46, GND48: SOLDER_PAD
HOUR0, HOUR1, HOUR2, HOUR3, HOUR4, HOUR5, HOUR6, HOUR7, HOUR8, HOUR9, HOUR10, HOUR11: LEDCHIPLED_0603; CHIPLED_0603
ICC1, ICC2, ICC3, ICC4: WS2811-SOP8; SO08-SKINNYPADS
ICH1, ICH2, ICH5, ICH6, ICH9, ICH10, ICH13, ICH14, ICH17, ICH18, ICH21, ICH22, ICH25, ICH26, ICH29, ICH30, ICH33, ICH34, ICH37, ICH41: WS2811-SOP8; SO08-SKINNYPADS
ICL3, ICL4, ICL7, ICL8, ICL11, ICL12, ICL15, ICL16, ICL19, ICL20, ICL23, ICL24, ICL27, ICL28, ICL31, ICL32, ICL35, ICL36, ICL39, ICL43: WS2811-SOP8; SO08-SKINNYPADS
MIN0, MIN1, MIN2, MIN3, MIN4, MIN5, MIN6, MIN7, MIN8, MIN9, MIN10, MIN11, MIN12, MIN13, MIN14, MIN15, MIN16, MIN17, MIN18, MIN19, MIN20, MIN21, MIN22, MIN23, MIN24, MIN25, MIN26, MIN27, MIN28, MIN29, MIN30, MIN31, MIN32, MIN33, MIN34, MIN35, MIN36, MIN37, MIN38, MIN39, MIN40, MIN41, MIN42, MIN43, MIN44, MIN45, MIN46, MIN47, MIN48, MIN49, MIN50, MIN51, MIN52, MIN53, MIN54, MIN55, MIN56, MIN57, MIN58, MIN59: LEDCHIPLED_0603; CHIPLED_0603
SEC0, SEC1, SEC2, SEC3, SEC4, SEC5, SEC6, SEC7, SEC8, SEC9, SEC10, SEC11, SEC12, SEC13, SEC14, SEC15, SEC16, SEC17, SEC18, SEC19, SEC20, SEC21, SEC22, SEC23, SEC24, SEC25, SEC26, SEC27, SEC28, SEC29, SEC30, SEC31, SEC32, SEC33, SEC34, SEC35, SEC36, SEC37, SEC38, SEC39, SEC40, SEC41, SEC42, SEC43, SEC44, SEC45, SEC46, SEC47, SEC48, SEC49, SEC50, SEC51, SEC52, SEC53, SEC54, SEC55, SEC56, SEC57, SEC58, SEC59: LEDCHIPLED_0603; CHIPLED_0603
TOUCH: SOLDER_PAD
U$2: TOUCH_PAD_LARGE

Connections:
5V: +5V.1, +5V1.1, HOUR0.A, HOUR1.A, HOUR2.A, HOUR3.A, HOUR4.A, HOUR5.A, HOUR6.A, HOUR7.A, HOUR8.A, HOUR9.A, HOUR10.A, HOUR11.A, ICC1.8 (VDD), ICC1.+5V (VDD), ICC2.8 (VDD), ICC2.+5V (VDD), ICC3.8 (VDD), ICC3.+5V (VDD), ICC4.8 (VDD), ICC4.+5V (VDD), ICH1.8 (VDD), ICH1.+5V (VDD), ICH2.8 (VDD), ICH2.+5V (VDD), ICH5.8 (VDD), ICH5.+5V (VDD), ICH6.8 (VDD), ICH6.+5V (VDD), ICH9.8 (VDD), ICH9.+5V (VDD), ICH10.8 (VDD), ICH10.+5V (VDD), ICH13.8 (VDD), ICH13.+5V (VDD), ICH14.8 (VDD), ICH14.+5V (VDD), ICH17.8 (VDD), ICH17.+5V (VDD), ICH18.8 (VDD), ICH18.+5V (VDD), ICH21.8 (VDD), ICH21.+5V (VDD), ICH22.8 (VDD), ICH22.+5V (VDD), ICH25.8 (VDD), ICH25.+5V (VDD), ICH26.8 (VDD), ICH26.+5V (VDD), ICH29.8 (VDD), ICH29.+5V (VDD), ICH30.8 (VDD), ICH30.+5V (VDD), ICH33.8 (VDD), ICH33.+5V (VDD), ICH34.8 (VDD), ICH34.+5V (VDD), ICH37.8 (VDD), ICH37.+5V (VDD), ICH41.8 (VDD), ICH41.+5V (VDD), ICL3.8 (VDD), ICL3.+5V (VDD), ICL4.8 (VDD), ICL4.+5V (VDD), ICL7.8 (VDD), ICL7.+5V (VDD), ICL8.8 (VDD), ICL8.+5V (VDD), ICL11.8 (VDD), ICL11.+5V (VDD), ICL12.8 (VDD), ICL12.+5V (VDD), ICL15.8 (VDD), ICL15.+5V (VDD), ICL16.8 (VDD), ICL16.+5V (VDD), ICL19.8 (VDD), ICL19.+5V (VDD), ICL20.8 (VDD), ICL20.+5V (VDD), ICL23.8 (VDD), ICL23.+5V (VDD), ICL24.8 (VDD), ICL24.+5V (VDD), ICL27.8 (VDD), ICL27.+5V (VDD), ICL28.8 (VDD), ICL28.+5V (VDD), ICL31.8 (VDD), ICL31.+5V (VDD), ICL32.8 (VDD), ICL32.+5V (VDD), ICL35.8 (VDD), ICL35.+5V (VDD), ICL36.8 (VDD), ICL36.+5V (VDD), ICL39.8 (VDD), ICL39.+5V (VDD), ICL43.8 (VDD), ICL43.+5V (VDD), MIN0.A, MIN1.A, MIN2.A, MIN3.A, MIN4.A, MIN5.A, MIN6.A, MIN7.A, MIN8.A, MIN9.A, MIN10.A, MIN11.A, MIN12.A, MIN13.A, MIN14.A, MIN15.A, MIN16.A, MIN17.A, MIN18.A, MIN19.A, MIN20.A, MIN21.A, MIN22.A, MIN23.A, MIN24.A, MIN25.A, MIN26.A, MIN27.A, MIN28.A, MIN29.A, MIN30.A, MIN31.A, MIN32.A, MIN33.A, MIN34.A, MIN35.A, MIN36.A, MIN37.A, MIN38.A, MIN39.A, MIN40.A, MIN41.A, MIN42.A, MIN43.A, MIN44.A, MIN45.A, MIN46.A, MIN47.A, MIN48.A, MIN49.A, MIN50.A, MIN51.A, MIN52.A, MIN53.A, MIN54.A, MIN55.A, MIN56.A, MIN57.A, MIN58.A, MIN59.A, SEC0.A, SEC1.A, SEC2.A, SEC3.A, SEC4.A, SEC5.A, SEC6.A, SEC7.A, SEC8.A, SEC9.A, SEC10.A, SEC11.A, SEC12.A, SEC13.A, SEC14.A, SEC15.A, SEC16.A, SEC17.A, SEC18.A, SEC19.A, SEC20.A, SEC21.A, SEC22.A, SEC23.A, SEC24.A, SEC25.A, SEC26.A, SEC27.A, SEC28.A, SEC29.A, SEC30.A, SEC31.A, SEC32.A, SEC33.A, SEC34.A, SEC35.A, SEC36.A, SEC37.A, SEC38.A, SEC39.A, SEC40.A, SEC41.A, SEC42.A, SEC43.A, SEC44.A, SEC45.A, SEC46.A, SEC47.A, SEC48.A, SEC49.A, SEC50.A, SEC51.A, SEC52.A, SEC53.A, SEC54.A, SEC55.A, SEC56.A, SEC57.A, SEC58.A, SEC59.A
GND: GND.1, GND46.1, GND48.1, ICC1.4 (GND), ICC1.GND, ICC2.4 (GND), ICC2.GND, ICC3.4 (GND), ICC3.GND, ICC4.4 (GND), ICC4.GND, ICH1.4 (GND), ICH1.GND, ICH2.4 (GND), ICH2.GND, ICH5.4 (GND), ICH5.GND, ICH6.4 (GND), ICH6.GND, ICH9.4 (GND), ICH9.GND, ICH10.4 (GND), ICH10.GND, ICH13.4 (GND), ICH13.GND, ICH14.4 (GND), ICH14.GND, ICH17.4 (GND), ICH17.GND, ICH18.4 (GND), ICH18.GND, ICH21.4 (GND), ICH21.GND, ICH22.4 (GND), ICH22.GND, ICH25.4 (GND), ICH25.GND, ICH26.4 (GND), ICH26.GND, ICH29.4 (GND), ICH29.GND, ICH30.4 (GND), ICH30.GND, ICH33.4 (GND), ICH33.GND, ICH34.4 (GND), ICH34.GND, ICH37.4 (GND), ICH37.GND, ICH41.4 (GND), ICH41.GND, ICL3.4 (GND), ICL3.GND, ICL4.4 (GND), ICL4.GND, ICL7.4 (GND), ICL7.GND, ICL8.4 (GND), ICL8.GND, ICL11.4 (GND), ICL11.GND, ICL12.4 (GND), ICL12.GND, ICL15.4 (GND), ICL15.GND, ICL16.4 (GND), ICL16.GND, ICL19.4 (GND), ICL19.GND, ICL20.4 (GND), ICL20.GND, ICL23.4 (GND), ICL23.GND, ICL24.4 (GND), ICL24.GND, ICL27.4 (GND), ICL27.GND, ICL28.4 (GND), ICL28.GND, ICL31.4 (GND), ICL31.GND, ICL32.4 (GND), ICL32.GND, ICL35.4 (GND), ICL35.GND, ICL36.4 (GND), ICL36.GND, ICL39.4 (GND), ICL39.GND, ICL43.4 (GND), ICL43.GND
unnamed: ICH1.1 (R), SEC59.C
unnamed: ICH1.3 (B), SEC1.C
unnamed: ICH1.2 (G), SEC0.C
unnamed: ICH2.1 (R), SEC2.C
unnamed: ICH2.2 (G), SEC3.C
unnamed: ICH2.3 (B), SEC4.C
unnamed: ICH5.1 (R), SEC5.C
unnamed: ICH5.2 (G), SEC6.C
unnamed: ICH5.3 (B), SEC7.C
unnamed: ICH6.1 (R), SEC8.C
unnamed: ICH6.2 (G), SEC9.C
unnamed: ICH6.3 (B), SEC10.C
unnamed: ICH13.1 (R), SEC17.C
unnamed: ICH9.1 (R), SEC11.C
unnamed: ICH9.2 (G), SEC12.C
unnamed: ICH9.3 (B), SEC13.C
unnamed: ICH26.2 (G), SEC39.C
unnamed: ICH10.1 (R), SEC14.C
unnamed: ICH10.2 (G), SEC15.C
unnamed: ICH10.3 (B), SEC16.C
unnamed: ICH14.1 (R), SEC20.C
unnamed: ICH13.2 (G), SEC18.C
unnamed: ICH13.3 (B), SEC19.C
unnamed: ICH14.2 (G), SEC21.C
unnamed: ICH14.3 (B), SEC22.C
unnamed: ICH26.3 (B), SEC40.C
unnamed: ICH17.1 (R), SEC23.C
unnamed: ICH17.2 (G), SEC24.C
unnamed: ICH17.3 (B), SEC25.C
unnamed: ICH18.1 (R), SEC26.C
unnamed: ICH18.2 (G), SEC27.C
unnamed: ICH18.3 (B), SEC28.C
unnamed: ICH29.5 (DO), ICH30.6 (DIN)
unnamed: ICH29.1 (R), SEC41.C
unnamed: ICH21.1 (R), SEC29.C
unnamed: ICH21.2 (G), SEC30.C
unnamed: ICH21.3 (B), SEC31.C
unnamed: ICH29.2 (G), SEC42.C
unnamed: ICH22.1 (R), SEC32.C
unnamed: ICH22.2 (G), SEC33.C
unnamed: ICH22.3 (B), SEC34.C
unnamed: ICH29.3 (B), SEC43.C
unnamed: ICH25.1 (R), SEC35.C
unnamed: ICH25.2 (G), SEC36.C
unnamed: ICH25.3 (B), SEC37.C
unnamed: ICH30.5 (DO), ICH33.6 (DIN)
unnamed: ICH26.1 (R), SEC38.C
unnamed: ICH30.1 (R), SEC44.C
unnamed: ICH30.2 (G), SEC45.C
unnamed: ICH30.3 (B), SEC46.C
unnamed: ICH33.5 (DO), ICH34.6 (DIN)
unnamed: ICH33.1 (R), SEC47.C
unnamed: ICH33.2 (G), SEC48.C
unnamed: ICH33.3 (B), SEC49.C
unnamed: ICH34.5 (DO), ICH37.6 (DIN)
unnamed: ICH34.1 (R), SEC50.C
unnamed: ICH34.2 (G), SEC51.C
unnamed: ICH34.3 (B), SEC52.C
unnamed: ICH37.5 (DO), ICH41.6 (DIN)
unnamed: ICH37.1 (R), SEC53.C
unnamed: ICH37.2 (G), SEC54.C
unnamed: ICH37.3 (B), SEC55.C
unnamed: ICH41.5 (DO), ICL3.6 (DIN)
unnamed: ICH41.1 (R), SEC56.C
unnamed: ICH41.2 (G), SEC57.C
unnamed: ICH41.3 (B), SEC58.C
unnamed: ICH1.5 (DO), ICH2.6 (DIN)
unnamed: ICH2.5 (DO), ICH5.6 (DIN)
unnamed: ICH5.5 (DO), ICH6.6 (DIN)
unnamed: ICH6.5 (DO), ICH9.6 (DIN)
unnamed: ICH9.5 (DO), ICH10.6 (DIN)
unnamed: ICH10.5 (DO), ICH13.6 (DIN)
unnamed: ICH13.5 (DO), ICH14.6 (DIN)
unnamed: ICH14.5 (DO), ICH17.6 (DIN)
unnamed: ICH17.5 (DO), ICH18.6 (DIN)
unnamed: ICH18.5 (DO), ICH21.6 (DIN)
unnamed: ICH21.5 (DO), ICH22.6 (DIN)
unnamed: ICH22.5 (DO), ICH25.6 (DIN)
unnamed: ICH25.5 (DO), ICH26.6 (DIN)
unnamed: ICH26.5 (DO), ICH29.6 (DIN)
unnamed: ICL3.1 (R), MIN59.C
unnamed: ICL3.2 (G), MIN0.C
unnamed: ICL3.3 (B), MIN1.C
unnamed: ICL4.1 (R), MIN2.C
unnamed: ICL4.2 (G), MIN3.C
unnamed: ICL4.3 (B), MIN4.C
unnamed: ICL7.1 (R), MIN5.C
unnamed: ICL7.2 (G), MIN6.C
unnamed: ICL7.3 (B), MIN7.C
unnamed: ICL8.1 (R), MIN8.C
unnamed: ICL8.2 (G), MIN9.C
unnamed: ICL8.3 (B), MIN10.C
unnamed: ICL3.5 (DO), ICL4.6 (DIN)
unnamed: ICL4.5 (DO), ICL7.6 (DIN)
unnamed: ICL11.1 (R), MIN11.C
unnamed: ICL11.2 (G), MIN12.C
unnamed: ICL11.3 (B), MIN13.C
unnamed: ICL7.5 (DO), ICL8.6 (DIN)
unnamed: ICL12.1 (R), MIN14.C
unnamed: ICL12.2 (G), MIN15.C
unnamed: ICL12.3 (B), MIN16.C
unnamed: ICL8.5 (DO), ICL11.6 (DIN)
unnamed: ICL15.1 (R), MIN17.C
unnamed: ICL15.2 (G), MIN18.C
unnamed: ICL15.3 (B), MIN19.C
unnamed: ICL11.5 (DO), ICL12.6 (DIN)
unnamed: ICL16.1 (R), MIN20.C
unnamed: ICL16.2 (G), MIN21.C
unnamed: ICL16.3 (B), MIN22.C
unnamed: ICL12.5 (DO), ICL15.6 (DIN)
unnamed: ICL19.1 (R), MIN23.C
unnamed: ICL19.2 (G), MIN24.C
unnamed: ICL19.3 (B), MIN25.C
unnamed: ICL15.5 (DO), ICL16.6 (DIN)
unnamed: ICL20.1 (R), MIN26.C
unnamed: ICL20.2 (G), MIN27.C
unnamed: ICL20.3 (B), MIN28.C
unnamed: ICL16.5 (DO), ICL19.6 (DIN)
unnamed: ICL23.1 (R), MIN29.C
unnamed: ICL23.2 (G), MIN30.C
unnamed: ICL23.3 (B), MIN31.C
unnamed: ICL19.5 (DO), ICL20.6 (DIN)
unnamed: ICL24.1 (R), MIN32.C
unnamed: ICL24.2 (G), MIN33.C
unnamed: ICL24.3 (B), MIN34.C
unnamed: ICL20.5 (DO), ICL23.6 (DIN)
unnamed: ICL27.1 (R), MIN35.C
unnamed: ICL27.2 (G), MIN36.C
unnamed: ICL27.3 (B), MIN37.C
unnamed: ICL23.5 (DO), ICL24.6 (DIN)
unnamed: ICL28.1 (R), MIN38.C
unnamed: ICL28.2 (G), MIN39.C
unnamed: ICL28.3 (B), MIN40.C
unnamed: ICL24.5 (DO), ICL27.6 (DIN)
unnamed: ICL31.1 (R), MIN41.C
unnamed: ICL31.2 (G), MIN42.C
unnamed: ICL31.3 (B), MIN43.C
unnamed: ICL27.5 (DO), ICL28.6 (DIN)
unnamed: ICL32.1 (R), MIN44.C
unnamed: ICL32.2 (G), MIN45.C
unnamed: ICL32.3 (B), MIN46.C
unnamed: ICL28.5 (DO), ICL31.6 (DIN)
unnamed: ICL35.1 (R), MIN47.C
unnamed: ICL35.2 (G), MIN48.C
unnamed: ICL35.3 (B), MIN49.C
unnamed: ICL31.5 (DO), ICL32.6 (DIN)
unnamed: ICL36.1 (R), MIN50.C
unnamed: ICL36.2 (G), MIN51.C
unnamed: ICL36.3 (B), MIN52.C
unnamed: ICL32.5 (DO), ICL35.6 (DIN)
unnamed: ICL39.1 (R), MIN53.C
unnamed: ICL39.2 (G), MIN54.C
unnamed: ICL39.3 (B), MIN55.C
unnamed: ICL35.5 (DO), ICL36.6 (DIN)
unnamed: ICL43.1 (R), MIN56.C
unnamed: ICL43.2 (G), MIN57.C
unnamed: ICL43.3 (B), MIN58.C
unnamed: ICL36.5 (DO), ICL39.6 (DIN)
unnamed: ICL39.5 (DO), ICL43.6 (DIN)
unnamed: DIN.1, ICH1.6 (DIN)
unnamed: HOUR11.C, ICC1.1 (R)
unnamed: HOUR0.C, ICC1.2 (G)
unnamed: HOUR1.C, ICC1.3 (B)
unnamed: DOUT.1, ICC4.5 (DO)
unnamed: HOUR2.C, ICC2.1 (R)
unnamed: HOUR3.C, ICC2.2 (G)
unnamed: HOUR4.C, ICC2.3 (B)
unnamed: HOUR5.C, ICC3.1 (R)
unnamed: HOUR6.C, ICC3.2 (G)
unnamed: HOUR7.C, ICC3.3 (B)
unnamed: HOUR8.C, ICC4.1 (R)
unnamed: HOUR9.C, ICC4.2 (G)
unnamed: HOUR10.C, ICC4.3 (B)
unnamed: ICC1.6 (DIN), ICL43.5 (DO)
unnamed: ICC1.5 (DO), ICC2.6 (DIN)
unnamed: ICC2.5 (DO), ICC3.6 (DIN)
unnamed: ICC3.5 (DO), ICC4.6 (DIN)
TOUCH: TOUCH.1, U$2.P$1, U$2.P$2

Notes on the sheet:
Touch

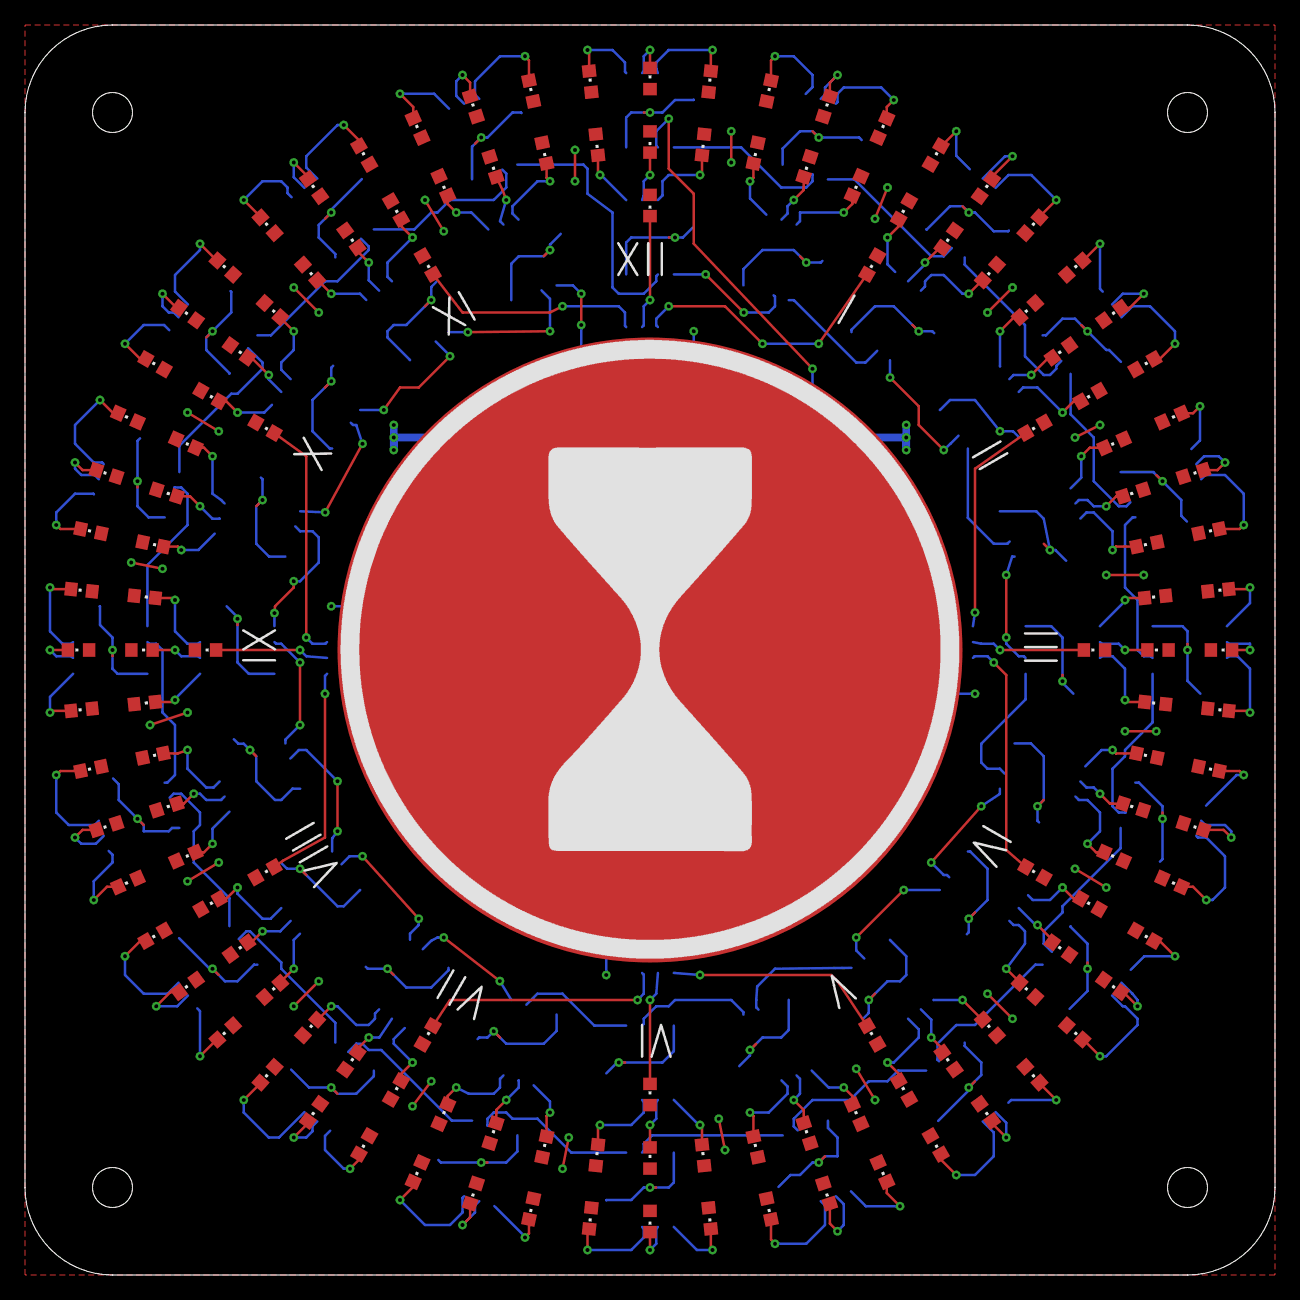
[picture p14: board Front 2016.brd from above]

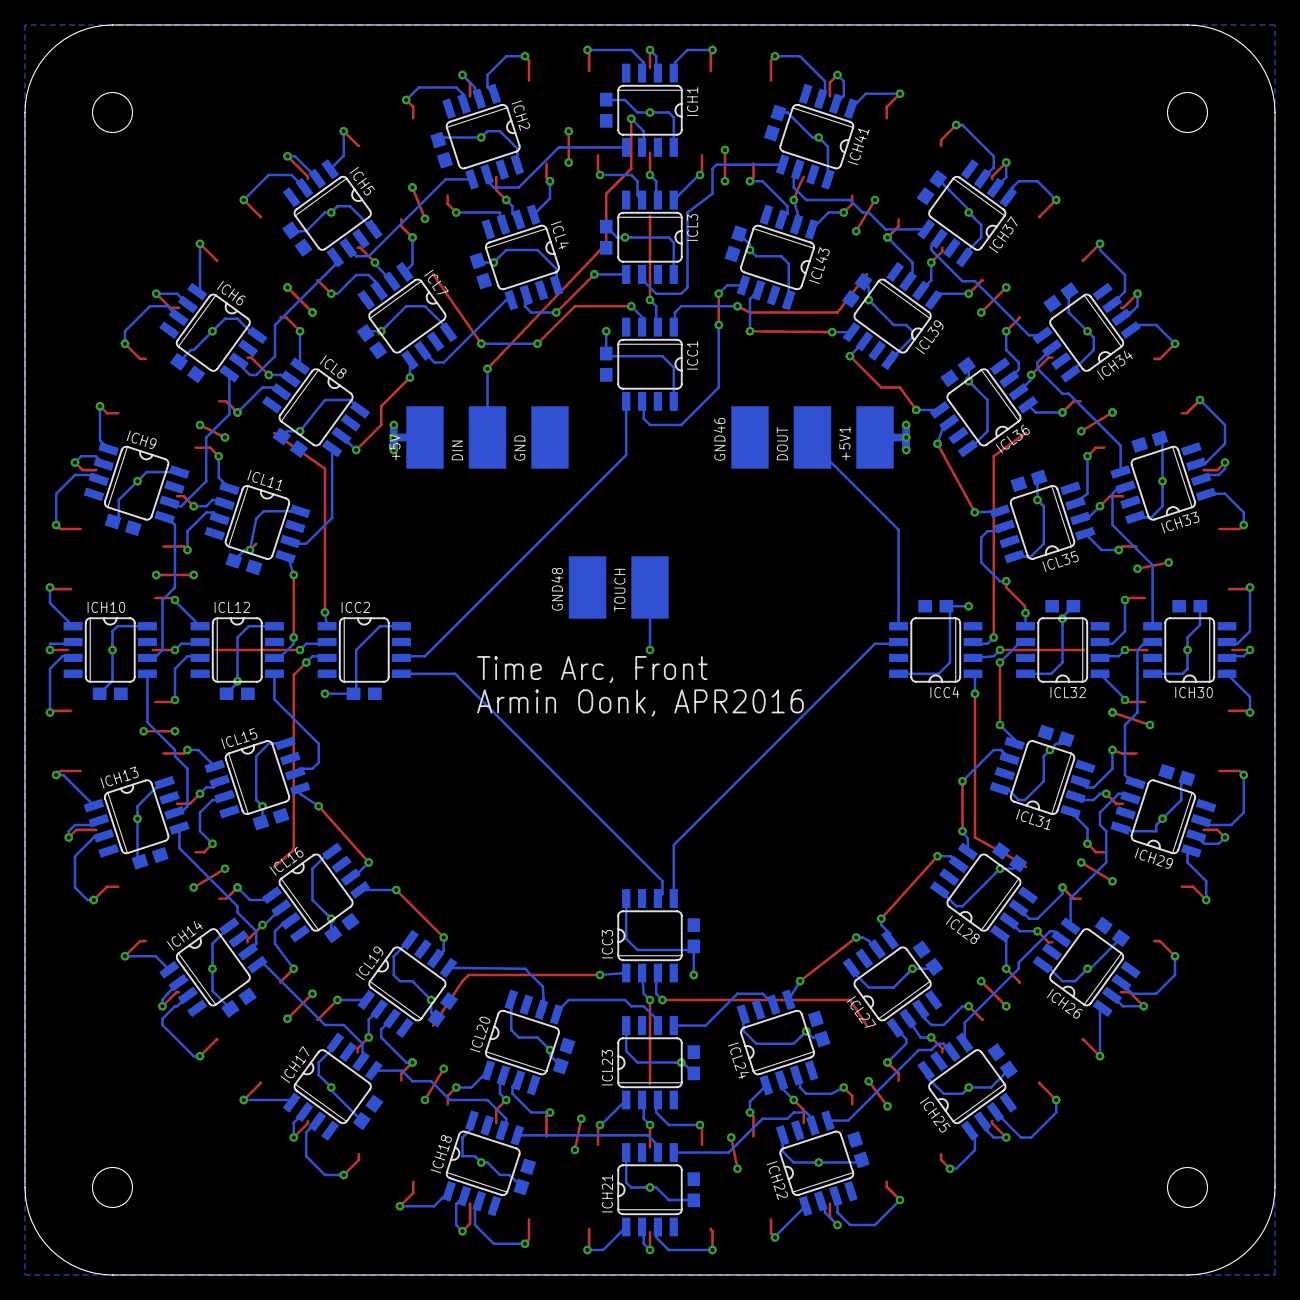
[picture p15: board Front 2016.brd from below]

Board: 2 copper layers, 100.0 x 100.0 mm, 187 parts (52 on the bottom side), 180 nets.

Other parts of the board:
U$1: TIMEARC_KEEPOUT
U$3: TIMEARC_LOGO_SIMPLE

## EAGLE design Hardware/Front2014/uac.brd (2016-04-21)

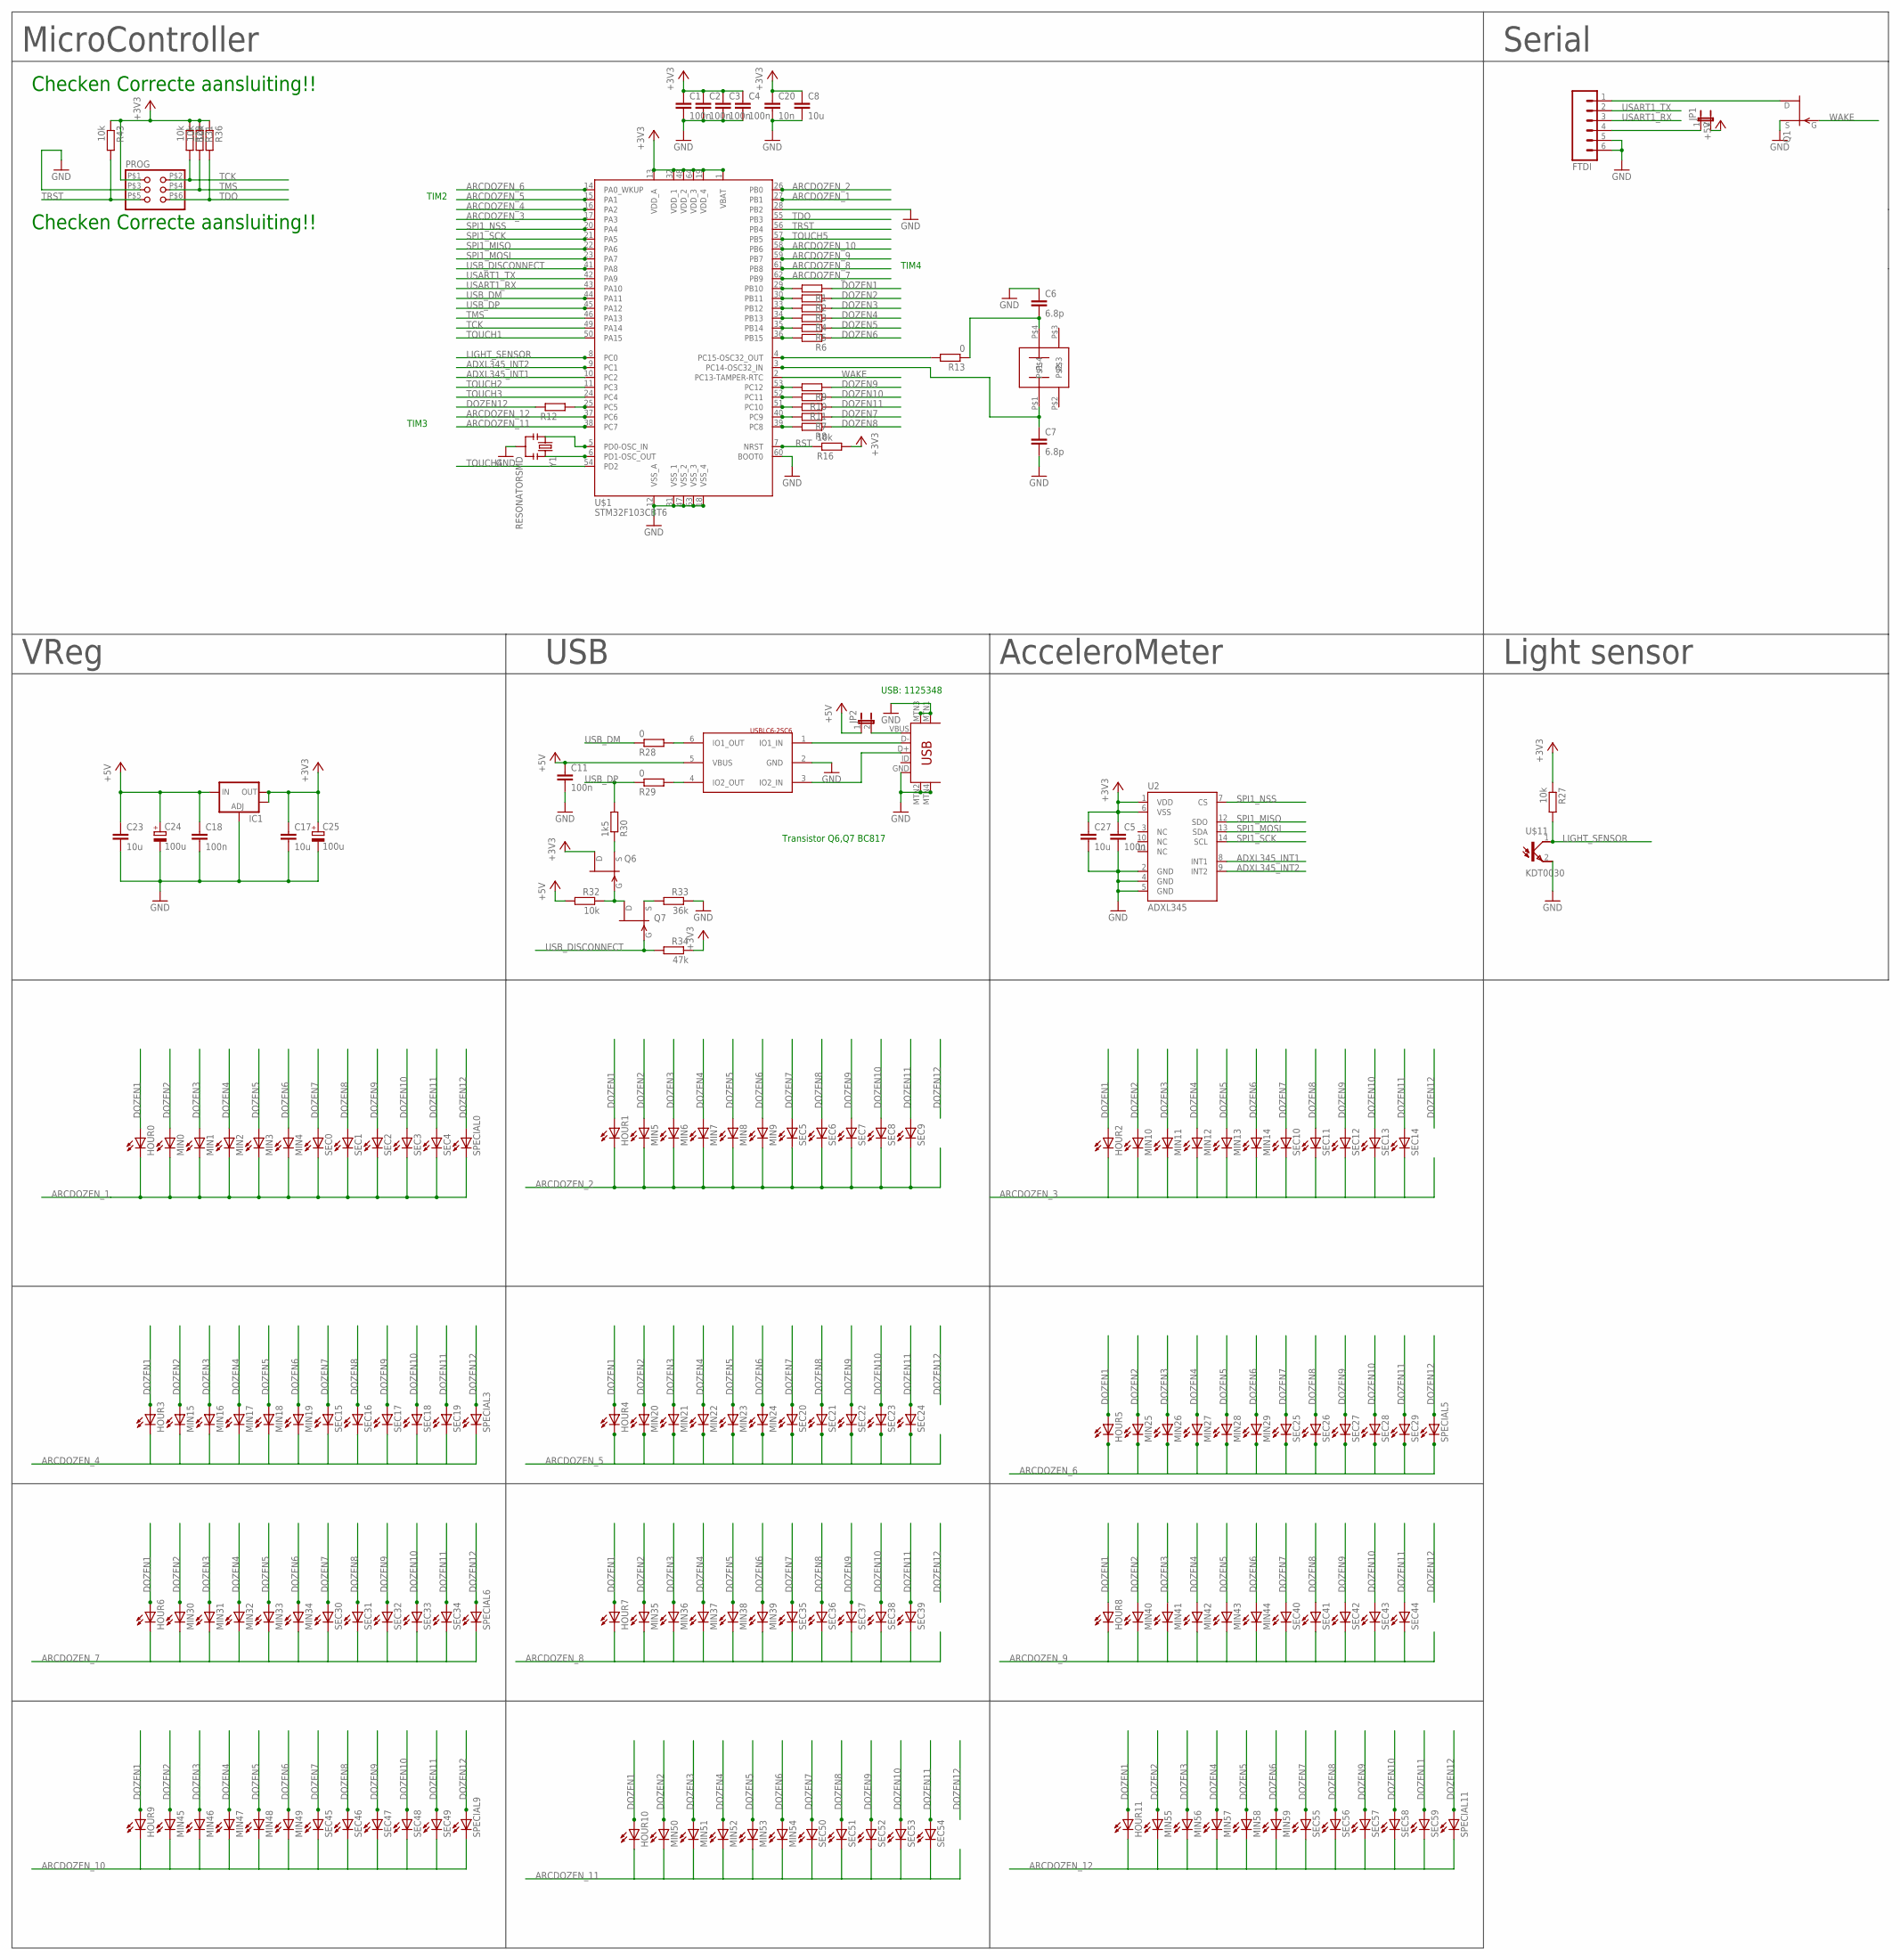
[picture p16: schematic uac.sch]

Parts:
C1, C2, C3, C4, C5, C11, C18: 100n; C0603
C6, C7: 6.8p; C0603
C8, C17, C23, C27: 10u; C0603
C20: 10n; C0603
C24, C25: 100u; SMC_C
FTDI: M06SMD; 1X06-SMD
HOUR0, HOUR1, HOUR2, HOUR3, HOUR4, HOUR5, HOUR6, HOUR7, HOUR8, HOUR9, HOUR10, HOUR11: LEDCHIPLED_0603; CHIPLED_0603
IC1: V_REG_LM1117SOT223; SOT223
JP1, JP2: JUMPER-2SMD-NO; SJ_2S-NO
MIN0, MIN1, MIN2, MIN3, MIN4, MIN5, MIN6, MIN7, MIN8, MIN9, MIN10, MIN11, MIN12, MIN13, MIN14, MIN15, MIN16, MIN17, MIN18, MIN19, MIN20, MIN21, MIN22, MIN23, MIN24, MIN25, MIN26, MIN27, MIN28, MIN29, MIN30, MIN31, MIN32, MIN33, MIN34, MIN35, MIN36, MIN37, MIN38, MIN39, MIN40, MIN41, MIN42, MIN43, MIN44, MIN45, MIN46, MIN47, MIN48, MIN49, MIN50, MIN51, MIN52, MIN53, MIN54, MIN55, MIN56, MIN57, MIN58, MIN59: LEDCHIPLED_0603; CHIPLED_0603
PROG: PINHD-2X3SMT; 2X03_SMT
Q1, Q6, Q7: 2N7002CK4SST; SOT23
R1, R2, R3, R4, R5, R6, R7, R8, R9, R10, R11, R12: R-EU_R0603; R0603
R13, R28, R29: 0; R0603
R16, R23, R27, R31, R32, R36, R43: 10k; R0603
R30: 1k5; R0603
R33: 36k; R0603
R34: 47k; R0603
SEC0, SEC1, SEC2, SEC3, SEC4, SEC5, SEC6, SEC7, SEC8, SEC9, SEC10, SEC11, SEC12, SEC13, SEC14, SEC15, SEC16, SEC17, SEC18, SEC19, SEC20, SEC21, SEC22, SEC23, SEC24, SEC25, SEC26, SEC27, SEC28, SEC29, SEC30, SEC31, SEC32, SEC33, SEC34, SEC35, SEC36, SEC37, SEC38, SEC39, SEC40, SEC41, SEC42, SEC43, SEC44, SEC45, SEC46, SEC47, SEC48, SEC49, SEC50, SEC51, SEC52, SEC53, SEC54, SEC55, SEC56, SEC57, SEC58, SEC59: LEDCHIPLED_0603; CHIPLED_0603
SPECIAL0, SPECIAL3, SPECIAL5, SPECIAL6, SPECIAL9, SPECIAL11: LEDCHIPLED_0603; CHIPLED_0603
U2: ADXL345; LGA14
U$1: STM32F103CBT6; LQFP64
U$2: CRYSTAL_32KHZ
U$11: KDT0030; FLD00030
U$12: USB-MINIB-5PIN; USB-MINIB
U$13: USBLC6-2SC6; SOT23
Y1: RESONATORSMD; RESONATOR-SMD

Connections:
+3V3: C1.1, C2.1, C3.1, C4.1, C5.1, C8.1, C17.1, C20.1, C25.+, C27.1, IC1.2 (OUT), IC1.4 (OUT), PROG.P$1 (1), Q6.3 (D), R16.2, R23.1, R27.1, R31.1, R34.1, R36.1, R43.1, U2.1 (VDD), U2.6 (VSS), U$1.1 (VBAT), U$1.13 (VDD_A), U$1.19 (VDD_4), U$1.32 (VDD_1), U$1.48 (VDD_2), U$1.64 (VDD_3)
+5V: C11.1, C18.1, C23.1, C24.+, IC1.3 (IN), JP1.2, JP2.1, R32.2, U$13.5 (VBUS)
ADXL345_INT1: U2.8 (INT1), U$1.10 (PC2)
ADXL345_INT2: U2.9 (INT2), U$1.9 (PC1)
ARCDOZEN_1: HOUR0.C, MIN0.C, MIN1.C, MIN2.C, MIN3.C, MIN4.C, SEC0.C, SEC1.C, SEC2.C, SEC3.C, SEC4.C, SPECIAL0.C, U$1.27 (PB1)
ARCDOZEN_2: HOUR1.C, MIN5.C, MIN6.C, MIN7.C, MIN8.C, MIN9.C, SEC5.C, SEC6.C, SEC7.C, SEC8.C, SEC9.C, U$1.26 (PB0)
ARCDOZEN_3: HOUR2.C, MIN10.C, MIN11.C, MIN12.C, MIN13.C, MIN14.C, SEC10.C, SEC11.C, SEC12.C, SEC13.C, SEC14.C, U$1.17 (PA3)
ARCDOZEN_4: HOUR3.C, MIN15.C, MIN16.C, MIN17.C, MIN18.C, MIN19.C, SEC15.C, SEC16.C, SEC17.C, SEC18.C, SEC19.C, SPECIAL3.C, U$1.16 (PA2)
ARCDOZEN_5: HOUR4.C, MIN20.C, MIN21.C, MIN22.C, MIN23.C, MIN24.C, SEC20.C, SEC21.C, SEC22.C, SEC23.C, SEC24.C, U$1.15 (PA1)
ARCDOZEN_6: HOUR5.C, MIN25.C, MIN26.C, MIN27.C, MIN28.C, MIN29.C, SEC25.C, SEC26.C, SEC27.C, SEC28.C, SEC29.C, SPECIAL5.C, U$1.14 (PA0_WKUP)
ARCDOZEN_7: HOUR6.C, MIN30.C, MIN31.C, MIN32.C, MIN33.C, MIN34.C, SEC30.C, SEC31.C, SEC32.C, SEC33.C, SEC34.C, SPECIAL6.C, U$1.62 (PB9)
ARCDOZEN_8: HOUR7.C, MIN35.C, MIN36.C, MIN37.C, MIN38.C, MIN39.C, SEC35.C, SEC36.C, SEC37.C, SEC38.C, SEC39.C, U$1.61 (PB8)
ARCDOZEN_9: HOUR8.C, MIN40.C, MIN41.C, MIN42.C, MIN43.C, MIN44.C, SEC40.C, SEC41.C, SEC42.C, SEC43.C, SEC44.C, U$1.59 (PB7)
ARCDOZEN_10: HOUR9.C, MIN45.C, MIN46.C, MIN47.C, MIN48.C, MIN49.C, SEC45.C, SEC46.C, SEC47.C, SEC48.C, SEC49.C, SPECIAL9.C, U$1.58 (PB6)
ARCDOZEN_11: HOUR10.C, MIN50.C, MIN51.C, MIN52.C, MIN53.C, MIN54.C, SEC50.C, SEC51.C, SEC52.C, SEC53.C, SEC54.C, U$1.38 (PC7)
ARCDOZEN_12: HOUR11.C, MIN55.C, MIN56.C, MIN57.C, MIN58.C, MIN59.C, SEC55.C, SEC56.C, SEC57.C, SEC58.C, SEC59.C, SPECIAL11.C, U$1.37 (PC6)
DOZEN1: HOUR0.A, HOUR1.A, HOUR2.A, HOUR3.A, HOUR4.A, HOUR5.A, HOUR6.A, HOUR7.A, HOUR8.A, HOUR9.A, HOUR10.A, HOUR11.A, R1.1
DOZEN2: MIN0.A, MIN5.A, MIN10.A, MIN15.A, MIN20.A, MIN25.A, MIN30.A, MIN35.A, MIN40.A, MIN45.A, MIN50.A, MIN55.A, R2.1
DOZEN3: MIN1.A, MIN6.A, MIN11.A, MIN16.A, MIN21.A, MIN26.A, MIN31.A, MIN36.A, MIN41.A, MIN46.A, MIN51.A, MIN56.A, R3.1
DOZEN4: MIN2.A, MIN7.A, MIN12.A, MIN17.A, MIN22.A, MIN27.A, MIN32.A, MIN37.A, MIN42.A, MIN47.A, MIN52.A, MIN57.A, R4.1
DOZEN5: MIN3.A, MIN8.A, MIN13.A, MIN18.A, MIN23.A, MIN28.A, MIN33.A, MIN38.A, MIN43.A, MIN48.A, MIN53.A, MIN58.A, R5.1
DOZEN6: MIN4.A, MIN9.A, MIN14.A, MIN19.A, MIN24.A, MIN29.A, MIN34.A, MIN39.A, MIN44.A, MIN49.A, MIN54.A, MIN59.A, R6.1
DOZEN7: R7.1, SEC0.A, SEC5.A, SEC10.A, SEC15.A, SEC20.A, SEC25.A, SEC30.A, SEC35.A, SEC40.A, SEC45.A, SEC50.A, SEC55.A
DOZEN8: R8.1, SEC1.A, SEC6.A, SEC11.A, SEC16.A, SEC21.A, SEC26.A, SEC31.A, SEC36.A, SEC41.A, SEC46.A, SEC51.A, SEC56.A
DOZEN9: R9.1, SEC2.A, SEC7.A, SEC12.A, SEC17.A, SEC22.A, SEC27.A, SEC32.A, SEC37.A, SEC42.A, SEC47.A, SEC52.A, SEC57.A
DOZEN10: R10.1, SEC3.A, SEC8.A, SEC13.A, SEC18.A, SEC23.A, SEC28.A, SEC33.A, SEC38.A, SEC43.A, SEC48.A, SEC53.A, SEC58.A
DOZEN11: R11.1, SEC4.A, SEC9.A, SEC14.A, SEC19.A, SEC24.A, SEC29.A, SEC34.A, SEC39.A, SEC44.A, SEC49.A, SEC54.A, SEC59.A
DOZEN12: R12.1, SPECIAL0.A, SPECIAL3.A, SPECIAL5.A, SPECIAL6.A, SPECIAL9.A, SPECIAL11.A
GND: C1.2, C2.2, C3.2, C4.2, C5.2, C6.1, C7.2, C8.2, C11.2, C17.2, C18.2, C20.2, C23.2, C24.-, C25.-, C27.2, FTDI.5, FTDI.6, IC1.1 (ADJ), PROG.P$3 (3), Q1.2 (S), R33.1, U2.2 (GND), U2.4 (GND), U2.5 (GND), U$1.12 (VSS_A), U$1.18 (VSS_4), U$1.28 (PB2), U$1.31 (VSS_1), U$1.47 (VSS_2), U$1.60 (BOOT0), U$1.63 (VSS_3), U$11.2 (EMI), U$12.GND, U$12.MTN1 (MTN2), U$12.MTN2 (MTN3), U$12.MTN3 (MTN1), U$12.MTN4, U$13.2 (GND), Y1.2
LIGHT_SENSOR: R27.2, U$1.8 (PC0), U$11.1 (COL)
unnamed: U$1.6 (PD1-OSC_OUT), Y1.3
unnamed: U$1.5 (PD0-OSC_IN), Y1.1
unnamed: JP2.2, U$12.VBUS
unnamed: R13.2, U$1.4 (PC15-OSC32_OUT)
unnamed: C6.2, R13.1, U$2.P$4
unnamed: C7.1, U$1.3 (PC14-OSC32_IN), U$2.P$1
unnamed: R1.2, U$1.29 (PB10)
unnamed: R2.2, U$1.30 (PB11)
unnamed: R3.2, U$1.33 (PB12)
unnamed: R4.2, U$1.34 (PB13)
unnamed: R5.2, U$1.35 (PB14)
unnamed: R6.2, U$1.36 (PB15)
unnamed: R7.2, U$1.40 (PC9)
unnamed: R8.2, U$1.39 (PC8)
unnamed: R9.2, U$1.53 (PC12)
unnamed: R10.2, U$1.52 (PC11)
unnamed: R11.2, U$1.51 (PC10)
unnamed: U$12.D-, U$13.1 (IO1_IN)
unnamed: FTDI.4, JP1.1
unnamed: FTDI.1, Q1.3 (D)
unnamed: U$12.D+, U$13.3 (IO2_IN)
unnamed: R12.2, U$1.25 (PC5)
unnamed: R28.2, U$13.6 (IO1_OUT)
unnamed: R29.2, U$13.4 (IO2_OUT)
unnamed: Q6.2 (S), R30.1
unnamed: Q6.1 (G), Q7.3 (D), R32.1
unnamed: Q7.2 (S), R33.2
RST: R16.1, U$1.7 (NRST)
SPI1_MISO: U2.12 (SDO), U$1.22 (PA6)
SPI1_MOSI: U2.13 (SDA), U$1.23 (PA7)
SPI1_NSS: U2.7 (CS), U$1.20 (PA4)
SPI1_SCK: U2.14 (SCL), U$1.21 (PA5)
TCK: PROG.P$2 (2), R23.2, U$1.49 (PA14)
TDO: PROG.P$6 (6), R36.2, U$1.55 (PB3)
TMS: PROG.P$4 (4), R31.2, U$1.46 (PA13)
TOUCH1: U$1.50 (PA15)
TOUCH2: U$1.11 (PC3)
TOUCH3: U$1.24 (PC4)
TOUCH4: U$1.54 (PD2)
TOUCH5: U$1.57 (PB5)
TRST: PROG.P$5 (5), R43.2, U$1.56 (PB4)
USART1_RX: FTDI.3, U$1.43 (PA10)
USART1_TX: FTDI.2, U$1.42 (PA9)
USB_DISCONNECT: Q7.1 (G), R34.2, U$1.41 (PA8)
USB_DM: R28.1, U$1.44 (PA11)
USB_DP: R29.1, R30.2, U$1.45 (PA12)
WAKE: Q1.1 (G), U$1.2 (PC13-TAMPER-RTC)

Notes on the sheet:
Checken Correcte aansluiting!!
TIM2
TIM4
VReg
MicroController
AcceleroMeter
Light sensor
Serial
USB
USB: 1125348
Transistor Q6,Q7 BC817
TIM3

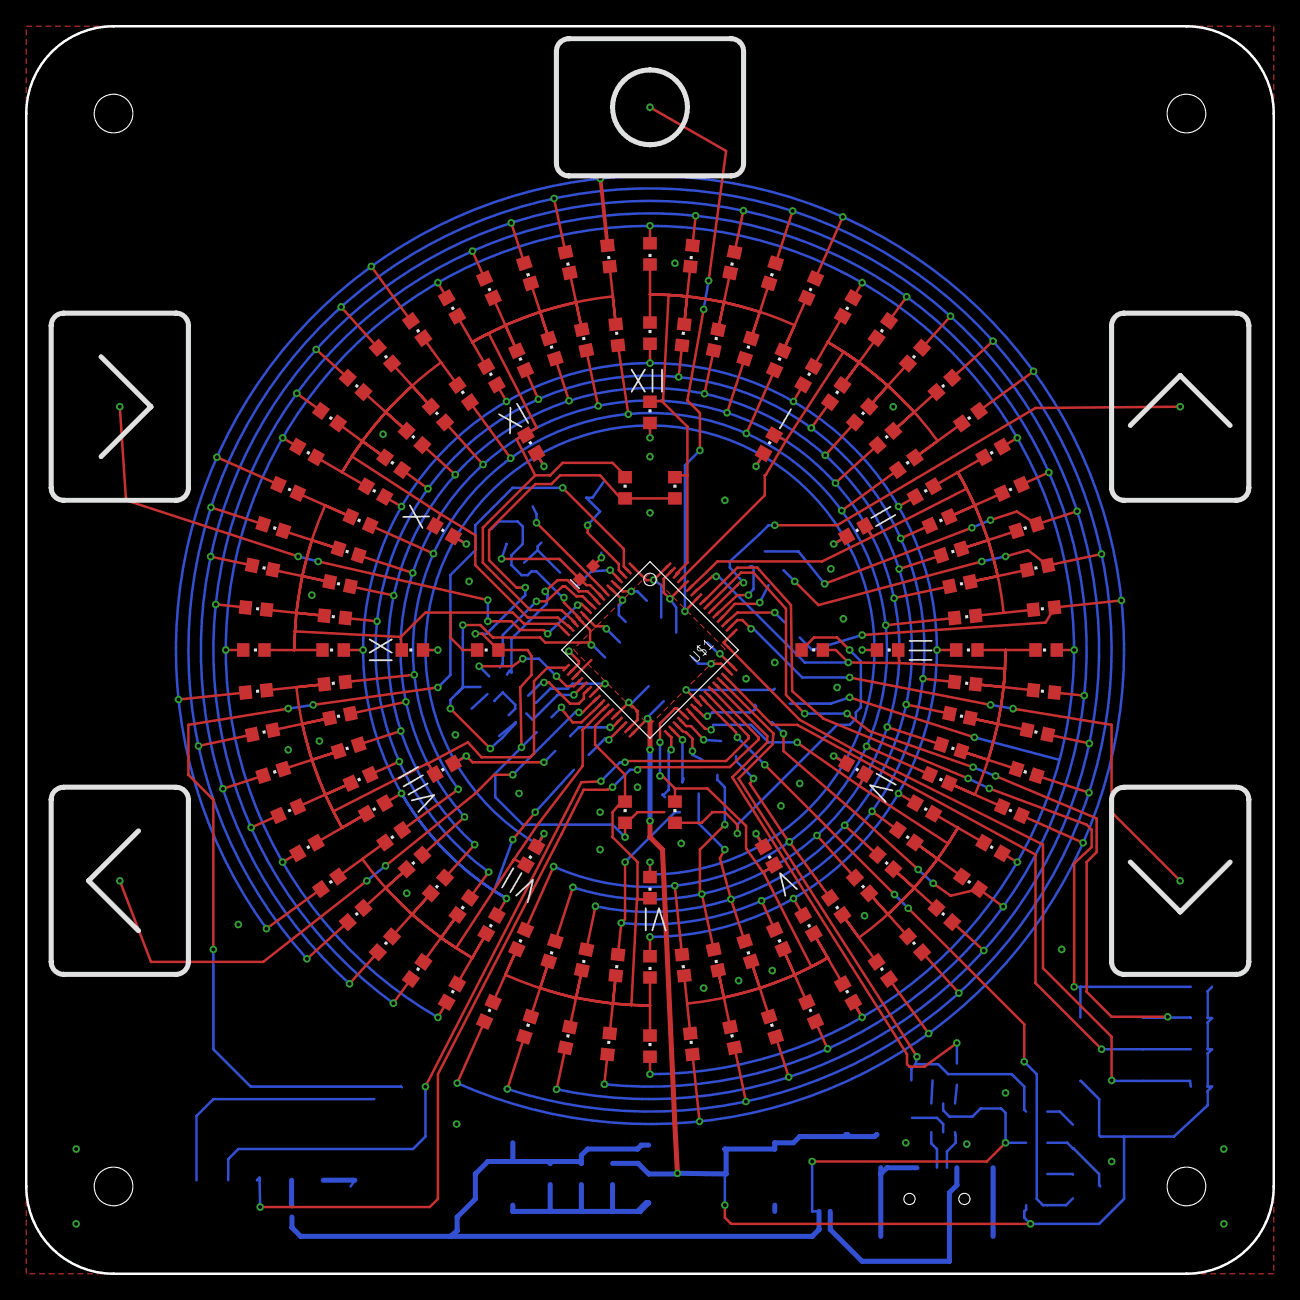
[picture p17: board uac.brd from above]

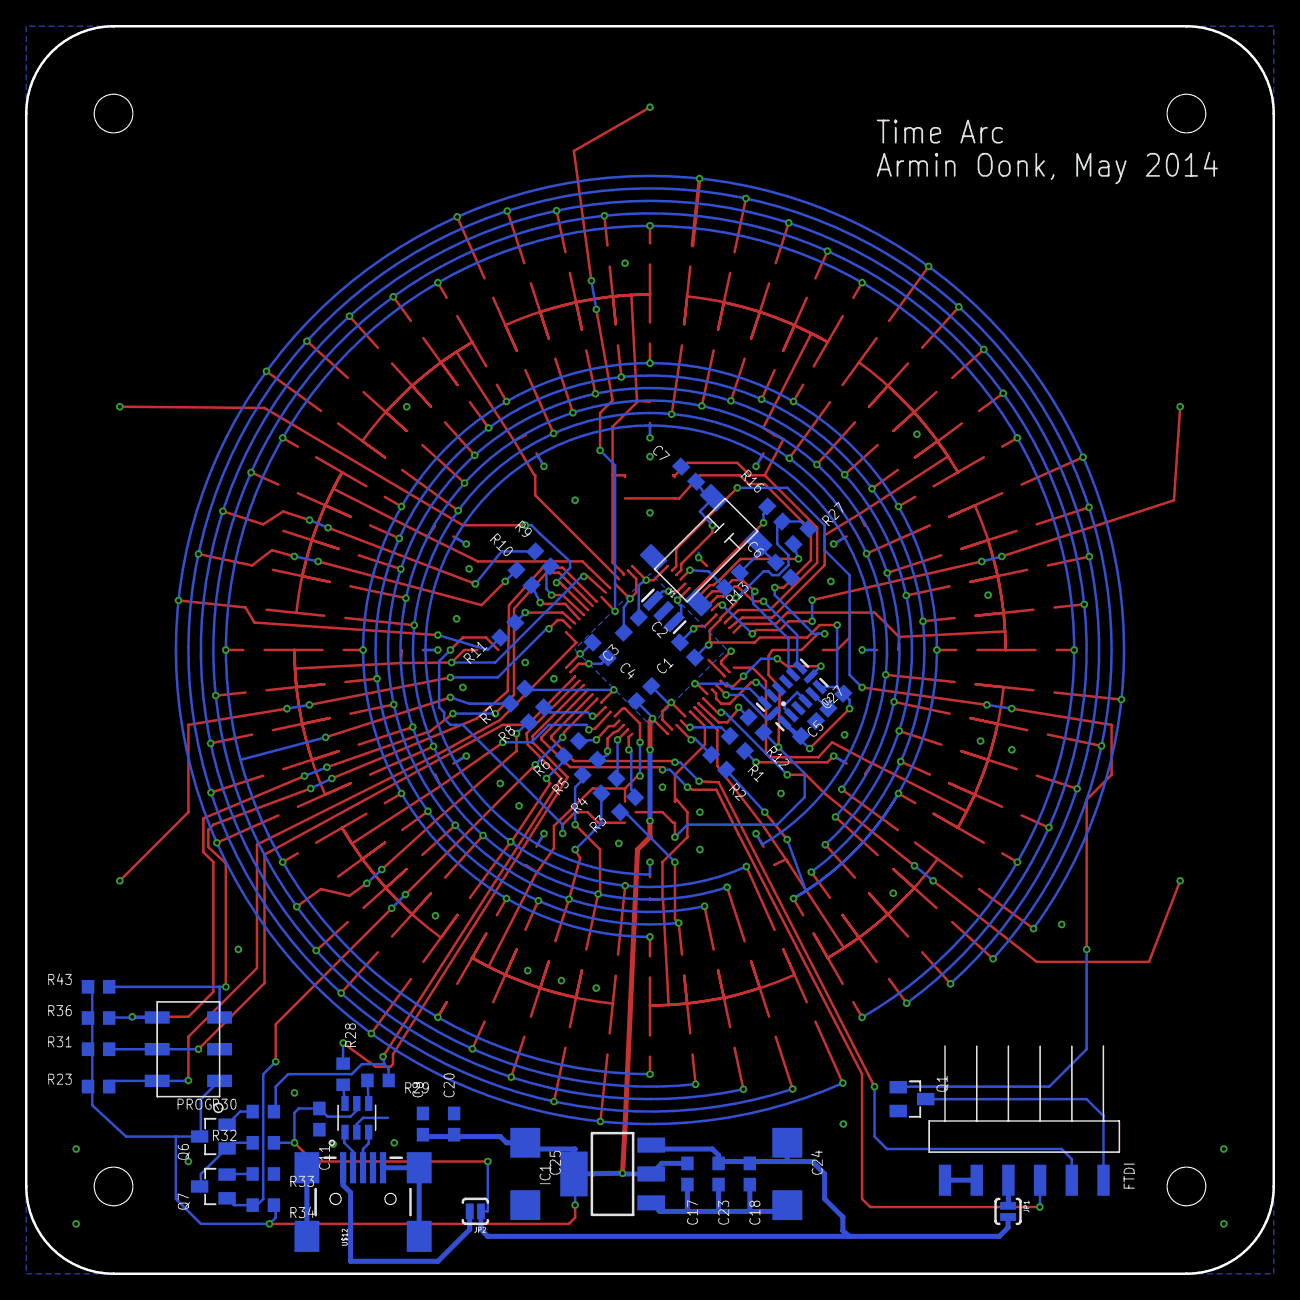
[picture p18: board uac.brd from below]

Board: 2 copper layers, 100.0 x 100.0 mm, 195 parts (54 on the bottom side), 72 nets.

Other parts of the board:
U$3: TIMEARC_KEEPOUT

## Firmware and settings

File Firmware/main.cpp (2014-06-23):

// STARTUP_FROM_RESET defineer  in project properties bij preprocessor definitions
// Dit slaat het programma permanent in de flash
#include "defines.h"
#include <stdio.h>
#include <string.h>
#include <ctl_api.h>
#include "main.h"

//FUNCTIONS
void ledHandler(void *p);
void ctl_delay(CTL_TIME_t t);
void initADC();
void initRTC();
void initUsart();
unsigned int readLight();
extern "C" int __putchar(char ch);
void handleTouch();
void printAutoMode();

CTL_TASK_t mainTask, ledTask, touchTask, comTask;
static unsigned ledTaskStack[256];
static unsigned touchTaskStack[256];
static unsigned comTaskStack[256];

displayBuffer display;

capTouch touchDown(GPIOC, GPIO_Pin_13);
capTouch touchRight(GPIOC, GPIO_Pin_3);
capTouch touchLeft(GPIOC, GPIO_Pin_4);
capTouch touchUp(GPIOD, GPIO_Pin_2);
capTouch touchTop(GPIOB, GPIO_Pin_5);
unsigned int ledCnt = 0;

//float light = 0;
adxl345 accel;
rtcClock rtc;
lightSensor light;

String completeData;
bool autoMode = true;
bool autoLight = true;
float manualLightVal = 0.0f;
int timeout = 0;
void comHandler(void *p)
{

  while(true)
  {
    if(completeData.length() > 0)
    {
        //Process data
        if(completeData.startsWith("TIME?"))
        {
          rtc.printTime();
        }
        else if(completeData.startsWith("TIME="))
        {
          String time = completeData.substring(completeData.indexOf("=")+1);
          time_t t = time.toInt();
          rtc.setTime(t);
        }
        else if(completeData.startsWith("OFFSET?"))
        {
          rtc.printOffset();
        }
        else if(completeData.startsWith("OFFSET="))
        {
          String tzString = completeData.substring(completeData.indexOf("=")+1);
          int offset = tzString.toInt();
          rtc.setOffset(offset);
        }
        else if(completeData.startsWith("POSE?"))
        {
          accel.print();
        }
        else if(completeData.startsWith("ID?"))
        {
          printf("ID=");
          for(int i=0; i<12; i++)
          {
            printf("%02x", *(const char *)(0x1FFFF7E8+i));
          }
          printf("\r\n");
        }
        else if(completeData.startsWith("MODE?"))
        {
          display.printMode();
        }
        else if(completeData.startsWith("MODE="))
        {
          String modeString = completeData.substring(completeData.indexOf("=")+1);
          if(modeString == "OFF")
          {
            display.setMode(OFF);
          }
          else if(modeString == "CLOCK")
          {
            display.setMode(CLOCK);
          }
          else if(modeString == "ANIMATION")
          {
            display.setMode(ANIMATION);
          }
        }
        else if(completeData.startsWith("AUTO?"))
        {
          printAutoMode();
        }
        else if(completeData.startsWith("AUTO="))
        {
          String autoString = completeData.substring(completeData.indexOf("=")+1);
          autoMode = (autoString == "TRUE");
          printAutoMode();
        }
        else if(completeData.startsWith("LIGHT?"))
        {
          printf("LIGHT=%0.2f\r\n", light.getValue());
        }
        else if(completeData.startsWith("LIGHT="))
        {
          String lightString = completeData.substring(completeData.indexOf("=")+1);
          if(lightString == "AUTO")
          {
            autoLight = true;
          }
          else
          {
            manualLightVal = lightString.toFloat();
            autoLight = false;
          }

        }
        else if(completeData.startsWith("TIMEOUT?"))
        {
          printf("TIMEOUT=%d\r\n",timeout);
        }
        else if(completeData.startsWith("TIMEOUT="))
        {
          String timeoutString = completeData.substring(completeData.indexOf("=")+1);
          timeout = timeoutString.toInt();
        }
        completeData = "";
    }
    ctl_delay(1);
  }
}

time_t lastUserActionTime = 0;
void ledHandler(void *p)
{
  CTL_TIME_t startupTime = ctl_get_current_time();

  ctl_delay(1000);
  accel.init();
 
  while(true)
  {
    handleTouch();

    accel.readAccel();

    // Get the last time the user was active
    if(accel.lastUserAction() > lastUserActionTime)
    {
      lastUserActionTime = accel.lastUserAction();
    }


    display.setPose(accel.pose);

    float lightVal = light.getValue();

    if(autoMode)
    {
      switch(accel.pose)
      {
        case FRONT:
        display.setMode(OFF);
        break;

        case BACK:
        display.setMode(ANIMATION);
        break;

        default:
        display.setMode(CLOCK);
        break;
      }
    }
    else
    {
      if(timeout != 0)
      {
        if((display.getMode() == CLOCK) && (rtc.getUTC() > (lastUserActionTime + timeout)))
        {
            display.setMode(OFF);
        }
        else if((display.getMode() == OFF) && (rtc.getUTC() < (lastUserActionTime + timeout)))
        {
          display.setMode(CLOCK);
        }
      }
    }

    if((display.getMode() == CLOCK))
    {
      display.setTime(rtc.getTime());
      if(autoLight)
      {
        display.setIntensity(lightVal);
      }
      else
      {
        display.setIntensity(manualLightVal);
      }
    }
    else if(display.getMode() == ANIMATION)
    {
      for(int i=0; i<totalNrLeds; i+=4)
      {
        display.ledOn(i+ledCnt%4);
      }
      display.setIntensity(1.0);
      display.switchBuffer();
    }

    ledCnt++;
    ctl_delay(100); 
  }
}

const int touchDelay = 50;
void touchHandler(void *p)
{
  touchDown.init();
  touchRight.init();
  touchLeft.init();
  touchUp.init();
  touchTop.init();

  while(true)
  {
    touchDown.start();
    ctl_delay(touchDelay);
    touchDown.stop();

    touchRight.start();
    ctl_delay(touchDelay);
    touchRight.stop();

    touchLeft.start();
    ctl_delay(touchDelay);
    touchLeft.stop();

    touchUp.start();
    ctl_delay(touchDelay);
    touchUp.stop();

    touchTop.start();
    ctl_delay(touchDelay);
    touchTop.stop();
  }
}

// MAIN
int main(void)
{
  SystemInit();
  RCC_PCLK1Config(RCC_HCLK_Div1); 
  
  RCC_APB2PeriphClockCmd(RCC_APB2Periph_AFIO, ENABLE);
 
  initGPIO();   // Configure GPIO
  initUsart();

  rtc.init();

  printf("\r\n");
  printf("start=%s %s\r\n", __DATE__, __TIME__);
  // CTL
  ctl_start_timer(ctl_increment_tick_from_isr);
  ctl_time_increment = 1;
  
  ctl_task_init(&mainTask, 255, "main");
  memset(ledTaskStack, 0xba, sizeof(ledTaskStack));
  memset(touchTaskStack, 0xba, sizeof(touchTaskStack));
  memset(comTaskStack, 0xba, sizeof(comTaskStack));

  // Make another task ready to run.
  ctl_task_run(&ledTask, 2, ledHandler, 0, "ledTask", sizeof(ledTaskStack) / sizeof(unsigned), ledTaskStack, 0);
  ctl_task_run(&touchTask, 3, touchHandler, 0, "touchTask", sizeof(touchTaskStack) / sizeof(unsigned), touchTaskStack, 0);
  ctl_task_run(&comTask, 1, comHandler, 0, "comTask", sizeof(comTaskStack) / sizeof(unsigned), comTaskStack, 0);
  // Now all the tasks have been created go to lowest priority.
  ctl_task_set_priority(&mainTask, 0);

  while(1)
  {
    if(ledTaskStack[0]  !=  0xbabababa)
      error("ledTaskStack Overflow!");
    if(touchTaskStack[0]  !=  0xbabababa)
      error("touchTaskStack Overflow!");
    if(comTaskStack[0]  !=  0xbabababa)
      error("comTaskStack Overflow!");
  }
}


void error(const char *err)
{
  while(true) //loop forever
  {
    printf("ERROR: %s\r\n", err);
    NVIC_SystemReset();
  }
}

void initGPIO(void)
{
  RCC_APB2PeriphClockCmd(RCC_APB2Periph_GPIOA, ENABLE);
  RCC_APB2PeriphClockCmd(RCC_APB2Periph_GPIOB, ENABLE);
  RCC_APB2PeriphClockCmd(RCC_APB2Periph_GPIOC, ENABLE);
  RCC_APB2PeriphClockCmd(RCC_APB2Periph_GPIOD, ENABLE);
  RCC_APB2PeriphClockCmd(RCC_APB2Periph_GPIOE, ENABLE);
  RCC_APB2PeriphClockCmd(RCC_APB2Periph_GPIOF, ENABLE);
  RCC_APB2PeriphClockCmd(RCC_APB2Periph_GPIOG, ENABLE);

  GPIO_InitTypeDef GPIO_InitStructure; 
  GPIO_StructInit(&GPIO_InitStructure);

}

void ctl_handle_error(CTL_ERROR_CODE_t error)
{
  //Do something
}

void ctl_delay(CTL_TIME_t t)
{
  ctl_timeout_wait(ctl_get_current_time()+t);
}

void initUsart()
{
  RCC_APB2PeriphClockCmd(RCC_APB2Periph_GPIOA, ENABLE);

  NVIC_InitTypeDef NVIC_InitStructure;
  NVIC_InitStructure.NVIC_IRQChannel                    = USART1_IRQn;
  NVIC_InitStructure.NVIC_IRQChannelPreemptionPriority  = 0x0f;
  NVIC_InitStructure.NVIC_IRQChannelSubPriority         = 0x0f;
  NVIC_InitStructure.NVIC_IRQChannelCmd                 = ENABLE;
  NVIC_Init(&NVIC_InitStructure);

  GPIO_InitTypeDef GPIO_InitStructure;
  GPIO_StructInit(&GPIO_InitStructure);
  GPIO_InitStructure.GPIO_Speed = GPIO_Speed_50MHz;

  GPIO_InitStructure.GPIO_Pin = GPIO_Pin_10;
  GPIO_InitStructure.GPIO_Mode = GPIO_Mode_IN_FLOATING;
  GPIO_Init(GPIOA, &GPIO_InitStructure);
  GPIO_InitStructure.GPIO_Pin = GPIO_Pin_9;
  GPIO_InitStructure.GPIO_Mode = GPIO_Mode_AF_PP;
  GPIO_Init(GPIOA, &GPIO_InitStructure);

  RCC_APB2PeriphClockCmd(RCC_APB2Periph_USART1, ENABLE); 

  USART_InitTypeDef USART_InitStructure;
  USART_InitStructure.USART_BaudRate = 230400;
  USART_InitStructure.USART_WordLength = USART_WordLength_8b;
  USART_InitStructure.USART_StopBits = USART_StopBits_1;
  USART_InitStructure.USART_Parity = USART_Parity_No;
  USART_InitStructure.USART_HardwareFlowControl = USART_HardwareFlowControl_None;
  USART_InitStructure.USART_Mode = USART_Mode_Rx | USART_Mode_Tx;
  
  // Configure USARTy
  USART_Init(USART1, &USART_InitStructure);
  USART_Cmd(USART1, ENABLE);

  USART_ITConfig(USART1, USART_IT_RXNE, ENABLE);
}

int __putchar(char ch)
{
  // Place your implementation of fputc here
  USART_SendData(USART1, (uint8_t) ch);

  /* Loop until the end of transmission */
  while (USART_GetFlagStatus(USART1, USART_FLAG_TC) == RESET)
  ;

  return ch;
}

unsigned int lastMenuTime = 0;
void handleTouch()
{
  // Reporting
  if(touchTop.isTouched())
  {
    printf("BUTTON=TOP\r\n");
    lastUserActionTime = rtc.getUTC();
  }
  
  if(touchRight.isTouched())
  {
    printf("BUTTON=RIGHT\r\n");
    lastUserActionTime = rtc.getUTC();
  }

  if(touchLeft.isTouched())
  {
    printf("BUTTON=LEFT\r\n");
    lastUserActionTime = rtc.getUTC();
  }

  if(touchUp.isTouched())
  {
    printf("BUTTON=UP\r\n");
    lastUserActionTime = rtc.getUTC();
  }

  if(touchDown.isTouched())
  {
    printf("BUTTON=DOWN\r\n");
    lastUserActionTime = rtc.getUTC();
  }
}

void printAutoMode()
{
  if(autoMode)
  {
    printf("AUTO=TRUE\r\n");
  }
  else
  {
    printf("AUTO=FALSE\r\n");
  }
}

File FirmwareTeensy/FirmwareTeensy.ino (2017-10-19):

#include "FastLED.h"
#define NUM_LEDS 56
#define DATA_PIN 17

CRGB leds[NUM_LEDS];

// receive
// 1 byte header 0x17
// 1 byte length
// 1 byte overall brightness
// 1 byte checksum
// 168 bytes led brightness data
// Total: 172 bytes
const int recvSize = 172;
byte recvBuffer[recvSize];
int recvCounter = 0;

void setup() {
  Serial2.begin(1000000);

  Serial.begin(115200);
  delay(1000);
  Serial.println("Start");

  // put your setup code here, to run once:
  FastLED.addLeds<NEOPIXEL, DATA_PIN>(leds, NUM_LEDS);
  FastLED.showColor(CHSV(50, 255, 255));
  FastLED.setCorrection(TypicalSMD5050);
  FastLED.setBrightness( 10 );
}

int loopCnt = 0;
float sliderFilt = 0.0f;
void loop() {

  while (Serial2.available() > 0) {
    byte c = Serial2.read();

    if (recvCounter == 0 ) {
      if (c == 0x17) {
        recvBuffer[recvCounter] = c;
        recvCounter++;
      }
    } else if(recvCounter == 1) {
      if(c == recvSize) {
        recvBuffer[recvCounter] = c;
        recvCounter++;
      } else {
        memset(recvBuffer, 0x00, recvSize);
        recvCounter = 0;
      }
    } else {
      recvBuffer[recvCounter] = c;
      recvCounter++;

      if(recvCounter == recvSize) {
        byte calcChecksum = 0x00;
        for(int i=0; i<recvSize; i++) {
          calcChecksum ^= recvBuffer[i];
        }

        if(calcChecksum == recvBuffer[3]) {
          Serial.println("Correct checksum");
          FastLED.setBrightness(recvBuffer[2]);
          for (int i = 0; i < NUM_LEDS; i++) {
            leds[i] = recvBuffer[i+4];
          }
          FastLED.show();
        }
      }
    }
  }
  
  // Turn the LED on, then pause
  CRGB current = CRGB::White;

  switch (loopCnt % 6) {
    case 0:
      current = CRGB::Red;
      break;

    case 1:
      current = CRGB::Green;
      break;

    case 2:
      current = CRGB::Blue;
      break;

    case 3:
      current = CRGB::Yellow;
      break;

    case 4:
      current = CRGB::Magenta;
      break;

    case 5:
      current = CRGB::Cyan;
      break;
  }

  for (int i = 0; i < NUM_LEDS; i++) {
    leds[i] = current;
  }

  //leds[12] = CRGB::White;
  FastLED.show();

  delay(500);
  // Now turn the LED off, then pause
  for (int i = 0; i < 12; i++) {
    leds[i] = CRGB::Black;
  }

  //leds[12] = CRGB::Black;
  FastLED.show();
  delay(500);

  Serial.println("Loop: " + String(loopCnt));
  loopCnt++;
}

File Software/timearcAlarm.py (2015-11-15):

#!/usr/bin/python
from threading import Timer
from datetime import datetime, timedelta
import math

import timearcGoogleCalendar
from timearcPrivate import *

import logging, logging.handlers
logger = logging.getLogger('TimeArc.Alarm')
logger.setLevel(logging.DEBUG)

class TimeArcAlarm:

	def printCountDownTime(self, secRemaining):
		secRemaining = round(secRemaining)
		# Seconds remaining
		seconds = math.floor(secRemaining%60)
		secRemaining = secRemaining/60
		# Minutes remainging
		minutes = math.floor(secRemaining%60)
		secRemaining = secRemaining/60
		# Hours Remaining
		hours = math.floor(secRemaining%24)
		secRemaining = secRemaining/24
		# Days remaining
		days = math.floor(secRemaining)
		
		retStr = "{:0>2d}".format(int(hours)) + ":" + "{:0>2d}".format(int(minutes)) + ":" + "{:0>2d}".format(int(seconds))
		if days > 0:
			retStr = str(days) + " days " + retStr
		
		return retStr
	
	def setTime(self, timestamp):
		tz = datetime.fromtimestamp(timestamp)
		dt = self.diffSeconds(tz)
		if dt > 0:
			self.triggerTime = tz
			self.alarmSet = True
			self.update()

	def stopAlarm(self):
		self.alarmSet = False
		
	def update(self):		
		dt = self.diffSeconds(self.triggerTime)
		
		timeRemaining = ""
		if self.alarmSet:
			if dt < 0:
				self.stopAlarm()
				self.callback()
		
			timeRemaining = "time remaining: " + self.printCountDownTime(dt)

		if dt > self.interval or dt <= 0:
			dt = self.interval
			
		logger.debug("Alarm update: " + timeRemaining + " checking again in: " + str(dt) + " seconds")

		self.alarmTimer = Timer(dt, self.update)
		self.alarmTimer.start()
		
		# Checking for new events
		dtCal = abs(self.diffSeconds(self.calCheckTime))
		logger.debug("Seconds since last google calendar check: " + str(dtCal))
		if dtCal > 300:
			self.calCheckTime = datetime.now()
			self.checkCalendar()
		
	def __init__(self, callback, interValSec=60):
		self.interval = interValSec
		self.callback = callback
		self.alarmSet = False
		self.triggerTime = datetime.now()
		
		self.calCheckTime = datetime.now()
		self.cal = timearcGoogleCalendar.TimeArcGoogleCalendar(FLOW, API_KEY)
		self.checkCalendar()

		self.update()
		
	def diffSeconds(self, t):
		dt = t - datetime.now()
		return dt.total_seconds()

	def checkCalendar(self):
		try:
			t = self.cal.getNextAlarm()
			
			if t == None:
				logger.info("Stopping the alarm, no event found")
				self.stopAlarm()
			else:
				logger.info("Google calendar callback, found event: " + str(t))
				self.setTime(t) 
		except:
			logger.exception('googleCallback')
			
		self.calCheckTime = datetime.now()

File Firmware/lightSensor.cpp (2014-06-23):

#include "lightSensor.h"

lightSensor::lightSensor()
{
  filter = 0.2;
  reset();

  RCC_ADCCLKConfig(RCC_PCLK2_Div6);
  RCC_APB2PeriphClockCmd(RCC_APB2Periph_ADC1, ENABLE);
  RCC_APB2PeriphClockCmd(RCC_APB2Periph_GPIOC, ENABLE);
  ADC_DeInit(ADC1);

  GPIO_InitTypeDef GPIO_InitStructure;
  GPIO_StructInit(&GPIO_InitStructure);
  GPIO_InitStructure.GPIO_Pin   = GPIO_Pin_0;
  GPIO_InitStructure.GPIO_Mode  = GPIO_Mode_AIN;
  GPIO_InitStructure.GPIO_Speed = GPIO_Speed_50MHz;
  GPIO_Init(GPIOC, &GPIO_InitStructure);

  ADC_InitTypeDef  ADC_InitStructure;
  ADC_InitStructure.ADC_Mode = ADC_Mode_Independent;
  ADC_InitStructure.ADC_ScanConvMode = DISABLE;
  ADC_InitStructure.ADC_ContinuousConvMode = DISABLE;
  ADC_InitStructure.ADC_ExternalTrigConv = ADC_ExternalTrigConv_None;
  ADC_InitStructure.ADC_DataAlign = ADC_DataAlign_Right;
  ADC_InitStructure.ADC_NbrOfChannel = 1;

  ADC_Init(ADC1, &ADC_InitStructure);

  ADC_RegularChannelConfig(ADC1, ADC_Channel_10, 1, ADC_SampleTime_239Cycles5);
  ADC_Cmd(ADC1, ENABLE);

  ADC_ResetCalibration(ADC1);
  // Check the end of ADC1 reset calibration register
  while(ADC_GetResetCalibrationStatus(ADC1));

  // Start ADC1 calibaration
  ADC_StartCalibration(ADC1);
  // Check the end of ADC1 calibration
  while(ADC_GetCalibrationStatus(ADC1));

  // Start ADC1 Software Conversion 
  ADC_SoftwareStartConvCmd(ADC1, ENABLE);
}

void lightSensor::reset()
{
  light = 4095.0;
}

unsigned int lightSensor::read()
{
  // Start the conversion
  ADC_SoftwareStartConvCmd(ADC1, ENABLE);
  // Wait until conversion completion
  while(ADC_GetFlagStatus(ADC1, ADC_FLAG_EOC) == RESET);
  // Get the conversion value
  return ADC_GetConversionValue(ADC1);
}

float lightSensor::getValue()
{
  light += 0.2*(read() - light);
  return (1.0-(light/4095.0));
}

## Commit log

2014-04-12 Arcdozen 2 toegevoegd
    [Angles.xlsx, uac.brd, uac.sch]
2014-04-13 Arcdozen arc
    [uac.brd]
2014-04-13 Leds aangesloten
    [uac.brd, uac.sch]
2014-04-13 New via
    [Angles.xlsx, uac.brd]
2014-04-13 Outer Vias
    [Angles.xlsx, uac.brd]
2014-04-13 arcdozen arcs
    [uac.brd]
2014-04-13 arcdozen traces
    [uac.brd]
2014-04-13 more traces
    [Angles.xlsx, uac.brd]
2014-04-13 traces leds complete (for now)
    [Angles.xlsx, uac.brd]
2014-04-14 Connected traces
    [uac.brd]
2014-04-14 Hour traces
    [uac.brd]
2014-04-14 4 layer
    [uac.brd]
2014-04-14 64 pin Micro geplaatst
    [uac.brd, uac.sch]
2014-04-14 32KHz crystal
    [uac.brd, uac.sch]
2014-04-15 Changed micro to stm32f103 144pins
    [uac.brd, uac.sch]
2014-04-15 connecting some leds
    [uac.brd, uac.sch]
2014-04-15 Moved silk to tdocu and rearranged arcdozen
    [uac.brd, uac.sch]
2014-04-16 Placing components, change to custom components
    [uac.brd, uac.sch]
2014-04-16 Start power subsystem
    [uac.brd, uac.sch]
2014-04-16 Drill size via's naar 0.31
    [uac.brd]
2014-04-19 Trying to get a 100x100mm board for ditypcb.com
    [uac.brd]
2014-04-19 Layout power system
    [uac.brd, uac.sch]
2014-04-19 Modified schematic, added adxl345
    [uac.brd, uac.sch]
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2014-04-19 Connected the accelerometer adxl345
    [uac.brd, uac.sch]
2014-04-19 Wake Up Leds 5mm
    [uac.brd, uac.sch]
2014-04-19 placed wake up light
    [uac.brd, uac.sch]
2014-04-20 Added cc3000 wifi
    [uac.brd, uac.sch]
2014-04-20 cc3300 on board
    [uac.brd, uac.sch]
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2014-04-21 Light sensor added, wifi connected to spi2
    [uac.brd, uac.sch]
2014-04-21 Debug serial port
    [uac.brd, uac.sch]
2014-04-21 usb added
    [uac.brd, uac.sch]
2014-04-21 placed USB
    [uac.brd, uac.sch]
2014-04-21 starting sound system
    [uac.brd, uac.sch]
2014-04-23 Audio amp added
    [uac.brd, uac.sch]
2014-04-25 Removed parts
    [uac.brd, uac.sch]
2014-04-25 Moved to 2 layer
    [uac.brd, uac.sch]
2014-04-25 64 pin microcontroller
    [uac.brd, uac.sch]
2014-04-25 connect led matrix
    [uac.brd, uac.sch]
2014-04-25 all within dimension lines
    [uac.brd, uac.sch]
2014-04-26 Board outline and mounting
    [MB913-BOM.xls, uac.brd, uac.sch]
2014-04-26 routing, rotated design 180
    [uac.brd]
2014-04-29 Touch pad
    [uac.brd]
2014-04-29 touch pad place
    [uac.brd]
2014-04-29 touch connected
    [uac.brd]
2014-04-29 last touch
    [uac.brd]
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2014-04-30 special connecten almost done
    [uac.brd, uac.sch]
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2014-05-05 added 3v3 to program header
    [uac.brd, uac.sch]
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2014-05-07 added spacer to BOM
    [uac BOM.xlsx]
2014-05-08 Added board outline to gerber
    [uac.brd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]
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2014-05-27 Moved everything to hardware folder
    [32khz ref MB672 BOM.csv, Angles.xlsx, MB913-BOM.xls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]
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2014-06-02 Hardware fix: hack wire connecting touchdown to PC13 Software fix: demo touch
    [capTouch.cpp, main.cpp]
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2014-06-12 Created keep out layer for lasercut
    [uac.brd, uac.sch]
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2014-06-19 Lasercut files as ordered on snijlab.nl
    [lasercutAssembly.dxf, lasercut_dxf_2004.dxf]
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2014-07-03 Waiting for correct time
    [timearc.py]
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2014-07-03 Added some extra timeout calls because it does not work
    [timearc.py]
2014-12-29 Fixed daylight saving time bug
    [timearc.py, timearcSerial.py]
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2015-05-05 Disabled decorator --> does not work yet. Using keep alive
    [timearc.py, timearcMPD.py, timearcSerial.py]
2015-05-06 Fixed ols python2 exceptions
    [timearcSerial.py]
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2015-05-18 Using timestamp to set alarm time, fix double alarm callback?
    [timearc.py, timearcAlarm.py, timearcGoogleCalendar.py]
2015-12-23 Fixed pinguin radio links
    [timearc.py]
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2015-12-24 Subtracted bolt holes from 3d print part
    [Enclosure.skp]
2015-12-27 Improved standoff (keeps clear of programming port)
    [Enclosure.skp]
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2016-01-21 Side pcb with capacitive slider and enclosure
    [Enclosure.skp, TimearcSides.brd, TimearcSides.sch]
2016-02-10 Tweaked the board File.php Enclosure.skp jorrit ideas
    [Enclosure.skp, TimearcSides.brd]
2016-02-16 Raspbarry Pi zero mounting PCB
    [RPi.kicad_pcb, RPi.sch]
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2016-02-18 Added Teensy LC, Wake up light WS2812
    [RPi.sch]
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2016-04-05 Fixed schematic/component errors
    [RPi.kicad_pcb, RPi.sch]
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2016-04-06 Trying to fix the teensyLC footprint
    [RPi.kicad_pcb, RPi.sch]
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2016-04-10 Placing the leds almost circular
    [RPi.kicad_pcb]
2016-04-11 Fixed first leds position wrong (Dirty hack)
    [RPi.kicad_pcb]
2016-04-12 Removed FTDI header, removed all unused footprints
    [RPi.kicad_pcb, RPi.sch]
2016-04-13 Placing stuff on the board
    [RPi.kicad_pcb, RPi.sch]
2016-04-13 Removed USB hub, ordered pcb
    [RPi.kicad_pcb, RPi.sch]
2016-04-16 Starting back pcb in eagle
    [back.brd, back.sch]
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2016-04-19 Added Teensy LC SMD version
    [Enclosure.skp, back.brd, back.sch]
2016-04-21 Start routing board Back2016/back.brd Added keep out to Front2014/uac.brd Tweaked the 3d print design
    [Enclosure.skp, back.brd, back.sch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]
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2016-04-23 Tweaked the silk screen
    [back.brd, back.sch]
2016-04-23 More small tweaks to the silkscreen
    [back.brd]
2016-04-25 Finished hardware design, added logo
    [back.brd]
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2016-04-25 Added TimeArc Back APR2016 BOM
    [Back APR2016 BOM.xlsx]
2016-04-25 Created an ulp to circular place on the BOTTOM (quick hack) Created schematic/board for a ws2811 driven front
    [Front 2016.brd, Front 2016.sch]
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2016-04-26 Connected rest of schematic, added solderpad for +5V, DIN, DOUT, GND Added a footprint for a capacitor in the ws8211 footprint
    [Front 2016.brd, Front 2016.sch]
2016-04-27 100% routed, Updated the TIMEARC_KEEPOUT footprint to include the 4 drill holes
    [Front 2016.brd, Front 2016.sch, back.brd]
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2016-04-27 Gerbers and last tweaks to the board
    [Front 2016.brd]
2016-04-27 Fixed missing stop mask in large touchpad Added artwork
    [Front 2016.brd, Front 2016.sch]
2016-05-03 Created the corner supports
    [Enclosure.skp, OrderDangerousPrototypes.skp]
2016-07-11 Creating version APR2016 of the back pcb
    [Back APR2016 BOM.xlsx, back.brd, back.sch]
2016-07-11 Fixed stupid error in schematic
    [back.brd, back.sch]

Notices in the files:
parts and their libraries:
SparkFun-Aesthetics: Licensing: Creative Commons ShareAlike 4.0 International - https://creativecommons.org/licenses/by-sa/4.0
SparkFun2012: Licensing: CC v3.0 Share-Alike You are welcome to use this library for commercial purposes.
